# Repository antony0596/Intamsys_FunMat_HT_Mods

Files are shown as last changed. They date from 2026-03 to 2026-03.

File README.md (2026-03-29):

# Intamsys_FunMat_HT_Mods
Modern upgrades for the Intamsys Funmat HT

I bought a "broken down" Intamsys FunMat HT.

The original user could not get it to print reliably. After some iteration I determined it was due to bad first layers.

So far, I have replaced the original motherboard with a BTT Octopus Pro and the DM422S drivers with TMC2209 drivers, also from BTT.

Paired with a Raspberry Pi for Klipper.

I had originally configured it to use the mechanical switch in the toolhead assembly to work as a z-probe and leveraged it for mesh bed leveling, but the force required to trigger this mechanical switch was causing massive dips in the rear corners. With a bed mesh range as high as 4mm in some instances due to this. I came across Beacon H and saw that the contact probe requires 30g to actuate and figured this might cause a good replacement. Thinking that the eddy current wouldn't function well on the carbon fiber plate. However, I was pleasantly surprised.

Anyways, you're looking at a motherboard replacement, Klipper config, and Beacon H.

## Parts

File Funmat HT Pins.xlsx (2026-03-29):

Cable Label | Purpose | Notes
J27 | X driver | Removed cables from DM422S drivers and spliced directly from board to motor. Installed TMC2209 drivers on the BTT OctoPro
J28 | Y driver
J29 | Z driver
J30 | E driver | Motor3 header was not working on my board. Moved it to motor4
J21-5, J21-6 | HE Heater
J21-3, J21-4 | CH SSR | Connected to one of the HE terminals
J34 (including green wire) | Bed Heater Control | I made a 3-pin JST-XH connector and plugged it into the RGB header. The RGB header isn't set up for JST but the pin spacing is identical. Green is the control signal.
J7 | PT100 Thermistor | Connected the two leads to the center pins of a 4-pin JST-XH connector
J10 | Extruder Cooling Fan 5V | Don't forget to switch the jumper to configure it as 5V or you'll damage the fan
J14 | Part Cooling Fan 24V
J20 | Filament Fan 24V | This is the small fan that sits by the filament compartment. I did connect it to the board and configured it in Klipper, but honestly, I don't use it.
J15 | LED bar 24V | You can configure it as a fan and control the brightness in Klipper by changing "fan speed"
J13 | Bed NTC R25 122K BETA 4050
J11 | Chamber NTC R25 100K BETA 3950
J5 | X endstop
J8 | Y endstop
J6 | Z min endstop | Did not use
J9 | Z max endstop | Did not use
J203-4, J203-5 | Z-offset | Configured as Z-endstop and virtual probe. Virtual probe used for bed mesh
J203-2, J203-3 | Filament runout sensor | Plugged into an endstop on board

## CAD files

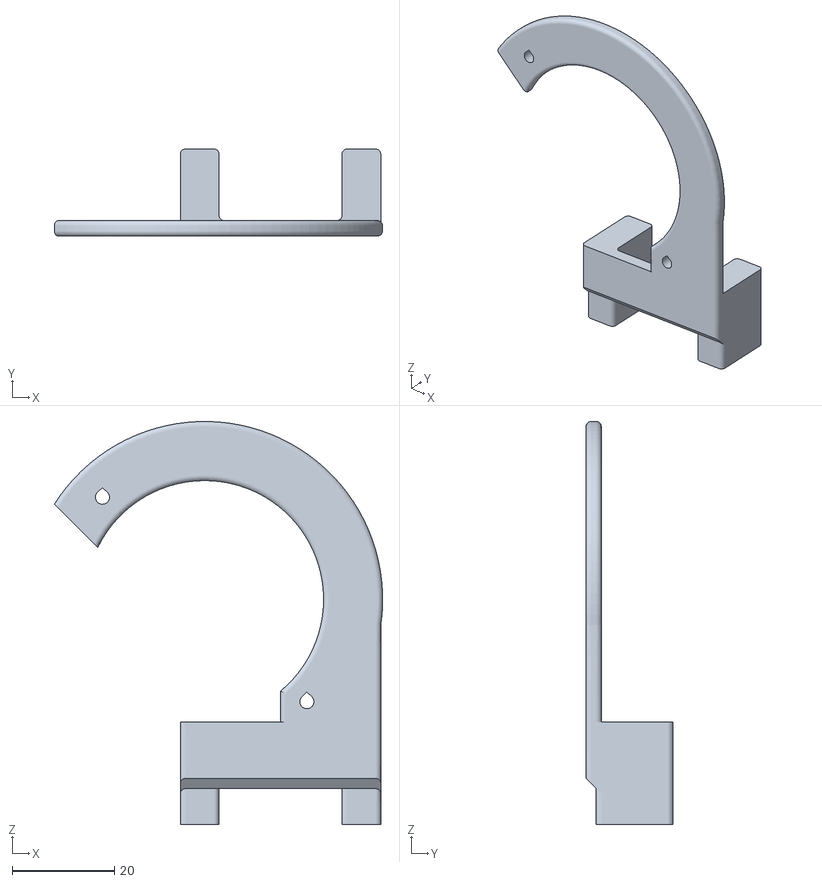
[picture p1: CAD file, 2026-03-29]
Beacon H LP Mount.stl
64.2 x 17.0 x 78.8

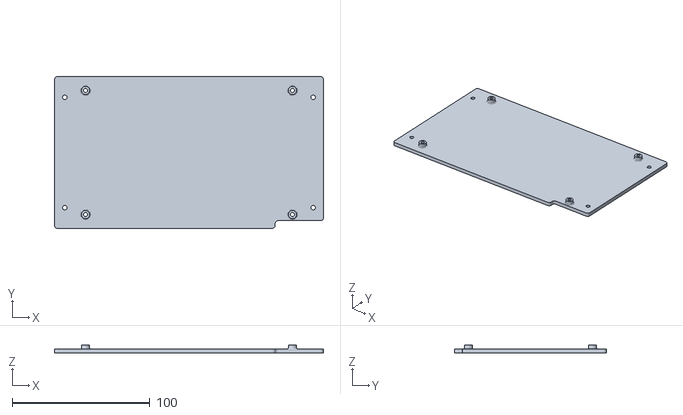
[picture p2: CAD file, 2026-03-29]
Funmat HT - Octo Pro Mounting Bracket.stl
195.0 x 110.0 x 6.00

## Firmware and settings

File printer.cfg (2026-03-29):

# STM32H723
# usb-Beacon_Beacon_RevH_<replace with your SN>-if00

[include mainsail.cfg]

[force_move]
enable_force_move: true

[screws_tilt_adjust]
screw1: 15,15
screw1_name: Front Left

screw2: 245,15
screw2_name: Front Right

screw3: 130,245
screw3_name: Rear Center

horizontal_move_z: 30
speed: 100

[beacon]
serial: /dev/serial/by-id/usb-Beacon_Beacon_RevH_<replace with your SN>-if00
x_offset: 20
y_offset: 15
mesh_main_direction: x
mesh_runs: 2
contact_max_hotend_temperature: 300

[safe_z_home]
home_xy_position: 130, 130
z_hop: 3

[bed_mesh]
speed: 200
horizontal_move_z: 3
mesh_min: 20, 15
mesh_max: 250, 240
probe_count: 10, 10
algorithm: bicubic

[input_shaper]
shaper_type_x: 2hump_ei
shaper_freq_x: 42.4
shaper_type_y: mzv
shaper_freq_y: 34.6
    
# Driver0
[stepper_x]
step_pin: PF13
dir_pin: !PF12
enable_pin: !PF14
microsteps: 16
rotation_distance: 40
endstop_pin: !PG6
position_endstop: 0
position_max: 260
homing_speed: 50

# Driver1
[stepper_y]
step_pin: PG0
dir_pin: PG1
enable_pin: !PF15
microsteps: 16
rotation_distance: 40
endstop_pin: !PG9
position_endstop: 0
position_max: 260
homing_speed: 50

# Driver2
[stepper_z]
step_pin: PF11
dir_pin: !PG3
enable_pin: !PG5
microsteps: 16
rotation_distance: 4
endstop_pin: probe:z_virtual_endstop
position_max: 260
position_min: -5
homing_speed: 5
second_homing_speed: 2
homing_retract_dist: 0 # beacon needs this to be set to 0

# Driver4
[extruder]
step_pin: PF9
dir_pin: PF10
enable_pin: !PG2
microsteps: 16
rotation_distance: 33.5
max_extrude_only_distance: 120
nozzle_diameter: 0.400
filament_diameter: 1.750
heater_pin: PA0 # HE0
sensor_pin:  PF8 # PT100 # RTD CS (onboard MAX31865)
spi_bus: spi1 # ChatGPT Suggestion
rtd_nominal_r: 100
rtd_reference_r: 430
sensor_type: MAX31865 # MAX31865 is built into Octopus Pro board and the T0 header hooks up to it
min_temp: 0
max_temp: 450

[resonance_tester]
accel_chip: beacon
probe_points: 130, 130, 30

[filament_switch_sensor material_0]
switch_pin: PG12

# custom thermistor to match the "Bed NTC R25 122K Beta 4050" label
[thermistor fht_bed_122k_4050]
temperature1: 25
resistance1: 122000
beta: 4050

[heater_bed]
heater_pin: PB10
sensor_pin: PF3
sensor_type: fht_bed_122k_4050
control: pid
min_temp: 0
max_temp: 160

[heater_generic chamber]
heater_pin: PB0
sensor_type: Generic 3950
sensor_pin: PF5

min_temp: 0
max_temp: 90
max_power: 1.0

# Chamber temp can be slow to rise due to wall mounted temp sensor.
# This gives it more time. 
[verify_heater chamber]
check_gain_time: 1200 # In seconds
hysteresis: 5 # Margin for error in degrees C
heating_gain: 1 # In degrees C
max_error: 120

[heater_fan hotend_fan]
pin: PA8
heater: extruder
heater_temp: 45.0
fan_speed: 1.0

# Part Cooling Fan
[fan]
pin: PE5
kick_start_time: 0.5

[fan_generic filament_fan]
pin: PD12
kick_start_time: 0.5

[fan_generic led_bar]
pin: PD13
kick_start_time: 0
off_below: 0.0
shutdown_speed: 0

[delayed_gcode led_startup]
initial_duration: 1
gcode:
    SET_FAN_SPEED FAN=led_bar SPEED=1.0

[mcu]
serial: /dev/serial/by-id/usb-Klipper_stm32h723xx_150009000851323235363233-if00

[printer]
kinematics: cartesian
max_velocity: 300
max_accel: 1400
max_z_velocity: 15
max_z_accel: 100

########################################
# TMC2209 configuration
########################################

[tmc2209 stepper_x]
uart_pin: PC4
run_current: 0.800
stealthchop_threshold: 999999

[tmc2209 stepper_y]
uart_pin: PD11
run_current: 0.800
stealthchop_threshold: 999999

[tmc2209 stepper_z]
uart_pin: PC6
run_current: 0.650
stealthchop_threshold: 999999

[tmc2209 extruder]
uart_pin: PF2
run_current: 0.800
stealthchop_threshold: 999999

[board_pins]
aliases:
    # EXP1 header
    EXP1_1=PE8, EXP1_2=PE7,
    EXP1_3=PE9, EXP1_4=PE10,
    EXP1_5=PE12, EXP1_6=PE13,    # Slot in the socket on this side
    EXP1_7=PE14, EXP1_8=PE15,
    EXP1_9=<GND>, EXP1_10=<5V>,

    # EXP2 header
    EXP2_1=PA6, EXP2_2=PA5,
    EXP2_3=PB1, EXP2_4=PA4,
    EXP2_5=PB2, EXP2_6=PA7,      # Slot in the socket on this side
    EXP2_7=PC15, EXP2_8=<RST>,
    EXP2_9=<GND>, EXP2_10=PC5

[exclude_object]

# Macros
[gcode_macro BYPASS_HOME_CHECK]
description: Force Klipper to treat current position as homed
gcode:
    RESPOND PREFIX="INFO" MSG="Bypassing home check - setting position to 0,0,0"
    SET_KINEMATIC_POSITION X=0 Y=0 Z=0

# We're naming this M191 (wait) to make it work with Orca Slicer filament chamber temp controls
# However, we're setting it to behave more like M141 (no wait) so that we can continue
# to heat up the bed as well, and speed up the overall process
[gcode_macro M191]
description: Set chamber temperature and continue (Marlin-style).
gcode:
    {% if 'S' not in params %}
        {action_raise_error("M191 requires S parameter")}
    {% endif %}
    {% set t = params.S|float %}

    SET_HEATER_TEMPERATURE HEATER=chamber TARGET={t}
    RESPOND PREFIX="INFO" MSG="Chamber heating to {t}C (no wait)"

[gcode_macro M141]
description: Set chamber temperature (no wait)
gcode:
    {% if 'S' not in params %}
        {action_raise_error("M141 requires S parameter")}
    {% endif %}
    SET_HEATER_TEMPERATURE HEATER=chamber TARGET={params.S|float}

#[gcode_macro SMART_BED_MESH]
#variable_retry_count: 0
#variable_max_retries: 2
#variable_threshold: 0.7
#gcode:
#    {% set retries = printer["gcode_macro SMART_BED_MESH"].retry_count|int %}
#    {% set max_retries = printer["gcode_macro SMART_BED_MESH"].max_retries|int %}
#    {% set threshold = printer["gcode_macro SMART_BED_MESH"].threshold|float %}
#
#    BED_MESH_CLEAR
#    BED_MESH_CALIBRATE
#
#    {% set mesh = printer.bed_mesh.mesh_matrix %}
#    {% if mesh is none %}
#        {action_respond_info("No mesh_matrix available after calibration; accepting mesh.")}
#        SET_GCODE_VARIABLE MACRO=SMART_BED_MESH VARIABLE=retry_count VALUE=0
#    {% else %}
#        {% set ns = namespace(vals=[]) %}
#        {% for row in mesh %}
#            {% for v in row %}
#                {% set ns.vals = ns.vals + [v|float] %}
#            {% endfor %}
#        {% endfor %}
#
#        {% set min_val = ns.vals|min %}
#        {% set max_val = ns.vals|max %}
#        {% set span = (max_val - min_val)|float %}
#
#        {action_respond_info("Mesh range: %.3f mm" % (span))}
#
#        {% if span > threshold and retries < max_retries %}
#            {action_respond_info("Range > %.3f mm; retrying (%d/%d)..." % (threshold, retries+1, max_retries))}
#            SET_GCODE_VARIABLE MACRO=SMART_BED_MESH VARIABLE=retry_count VALUE={retries + 1}
#            G4 P1000
#            SMART_BED_MESH
#        {% else %}
#            {action_respond_info("Mesh accepted.")}
#            SET_GCODE_VARIABLE MACRO=SMART_BED_MESH VARIABLE=retry_count VALUE=0
#        {% endif %}
#    {% endif %}
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

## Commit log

2026-03-29 Enhance README with upgrade details for FunMat HT
    Expanded the README with details about upgrades and modifications made to the Intamsys FunMat HT, including motherboard and driver replacements, and z-probing adjustments.
2026-03-29 printer.cfg configuration
    My printer.cfg configuration for klipper. Remember to update respective serial numbers for your board and beacon device. I'm using USB connections. If you plan to use something else, I assume you kno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
    [printer.cfg]
2026-03-29 Mounting bracket for MCU
    [Funmat HT - Octo Pro Mounting Bracket.stl]
2026-03-29 Pinout reference
    Gives a high level description of how I connected existing cables to Octo Pro board
    [Funmat HT Pins.xlsx]
2026-03-29 Mounting adapter for Beacon H LP
    [Beacon H LP Mount.stl]
